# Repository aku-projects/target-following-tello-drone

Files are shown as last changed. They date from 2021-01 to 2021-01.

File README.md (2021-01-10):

# Target following tello drone

## Intro
This repo contains code to provide tello drone the capability to follow any particular target using Sipeed maix bit board. ESP32 board is used as a communication bridge between external bluetooth app, maix bit board and tello.

As examples, the scripts added here allows the drone to follow green coloured object or raccoon for which a neural network was trained

For coloured objects the drone can align itself and move towards it.

For raccoon/object it can only detect and move towards it/follow it in straight line. This mainly was due to the viewing angle and size of the object causing detection issue. Probably better training can be done to make the object following more robust.

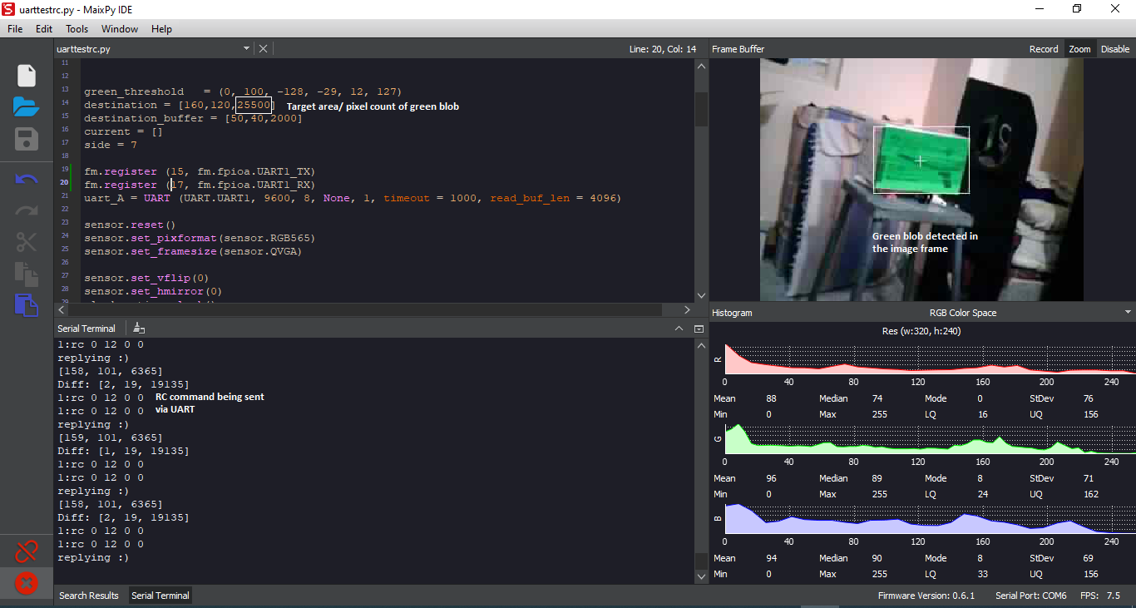
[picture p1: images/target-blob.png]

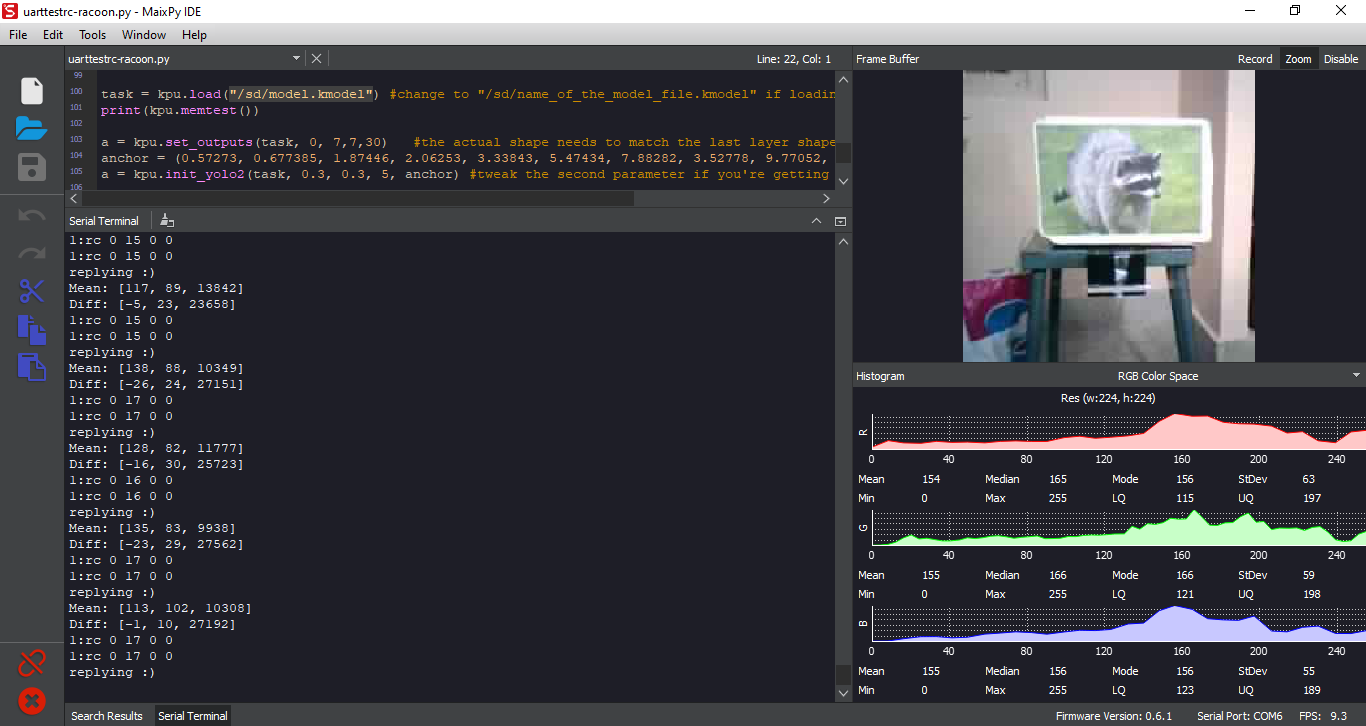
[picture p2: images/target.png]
 

## Setting up the drone

### Hardware assembly

#### Materials
1) Sipeed maix bit board (with camera) [link](https://www.seeedstudio.com/Sipeed-MAix-BiT-for-RISC-V-AI-IoT-p-2872.html)
2) ESP32 [link](https://www.amazon.com/HiLetgo-ESP-WROOM-32-Development-Microcontroller-Integrated/dp/B0718T232Z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)
3) Tello [link](https://www.amazon.com/Tello-CP-PT-00000252-01-Quadcopter-Drone/dp/B07H4W5YWB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)
4) boost converter [link](https://www.amazon.com/Comidox-Module-Voltage-Converter-0-9-5V/dp/B07L76KLRY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)
5) misc. (Wires, ziptie etc)

Mount the boards as shown in the image.  
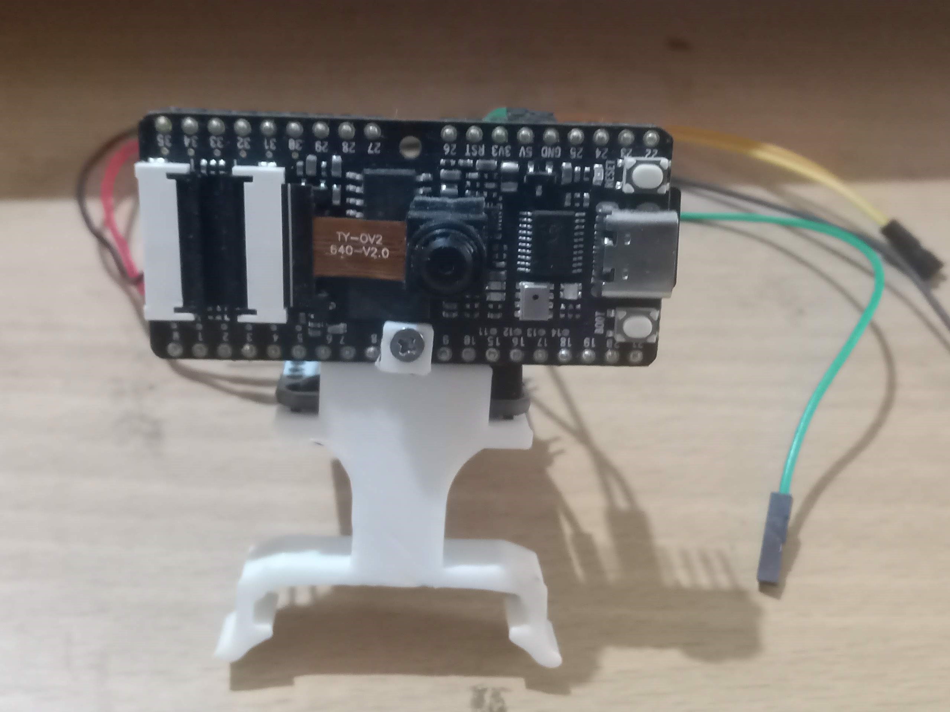
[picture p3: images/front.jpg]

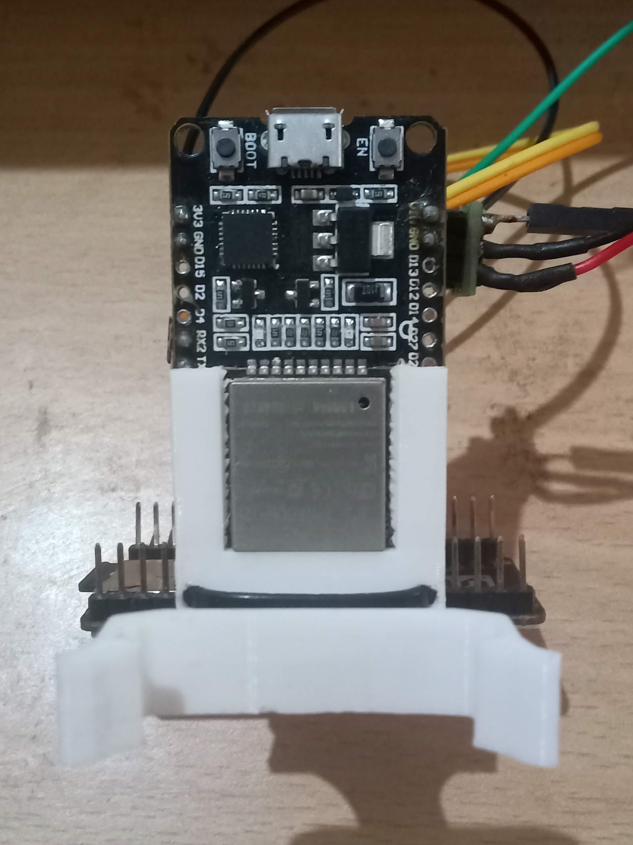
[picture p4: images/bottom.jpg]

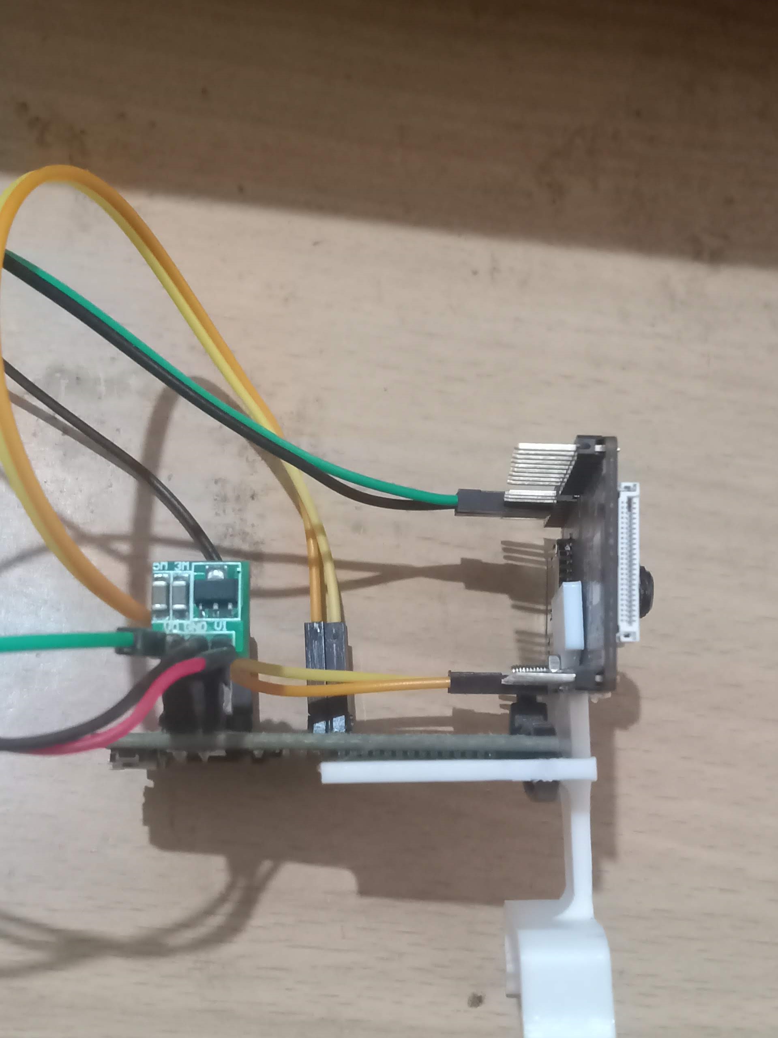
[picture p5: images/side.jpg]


Make uart connection between the Boards as follows

ESP32 GPIO 16 (UART 2 RX)<-> k210 GPIO 15 (UART 1 TX)  
ESP32 GPIO 17 (UART 2 TX)<-> k210 GPIO 17 (UART 1 RX)

Power the boards using boost converter if using 3.7 volts. For this project the 3.7 volts was tapped from on board battery.

Snap the assembly onto the tello drone
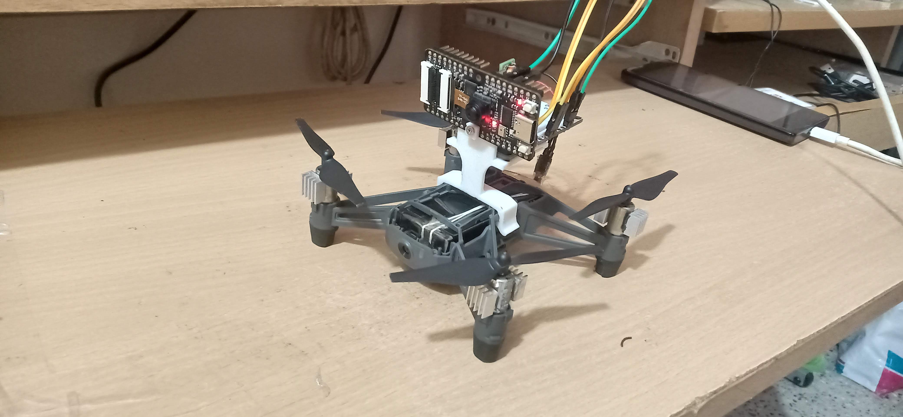
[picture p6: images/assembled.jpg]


### Software 

Create custom buttons on [Serial Bluetooth terminal app](https://play.google.com/store/apps/details?hl=en&id=de.kai_morich.serial_bluetooth_terminal) as follows:
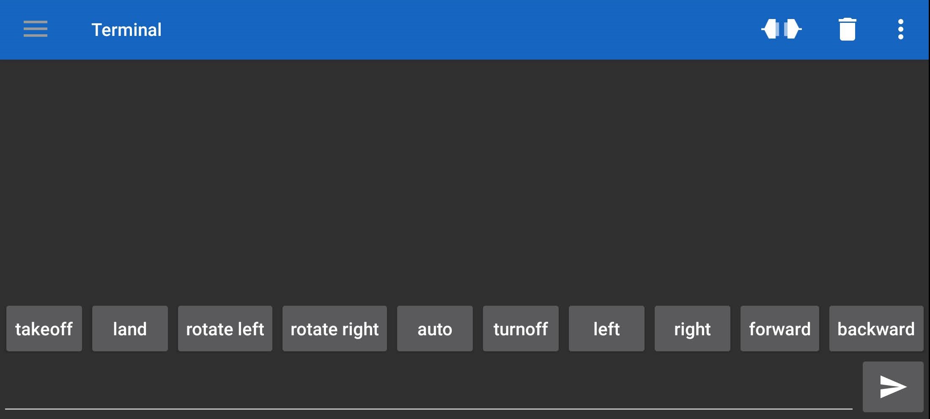
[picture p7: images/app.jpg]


add hex values for each starting from 0 ie takeoff = hex value 0, land = hex value 1, ...etc   
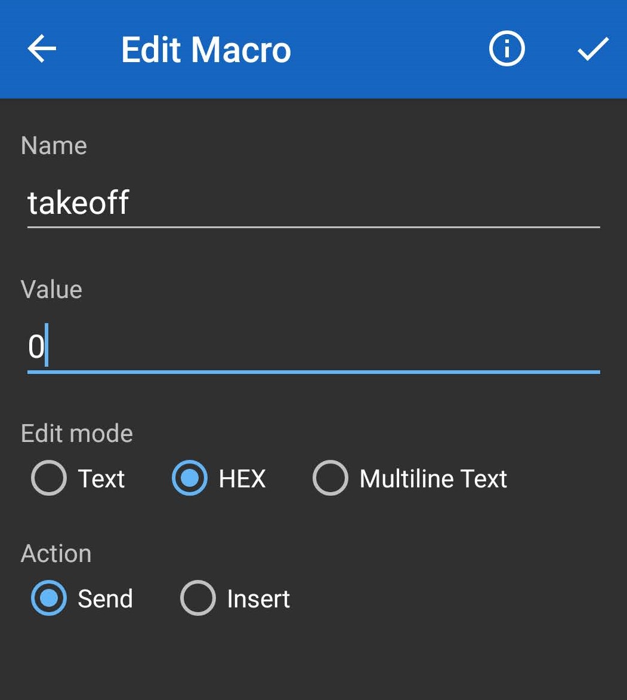
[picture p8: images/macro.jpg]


Add tello library needed by ESP32 to control the drone. [Link](https://github.com/aku-projects/ESP32-Tello)

Modify the tello wifi credentials in .ino file under resources > code > esp32 and program the same into the board.

Set up the Sipeed maix bit board based on the instructions [here.](https://maixpy.sipeed.com/en/)

Now open the micropython script in resources > code > k210 using maix py ide and save the same to the board.

use tello_rc_bt_wifi.ino and uarttestrc.[]()py for coloured object following

use tello_rc_bt_wifi_no_dest.ino and uarttestrc-racoon.[]()py for racoon following.
## Running the Code

Power up the tello drone and the boards. Connect to ESP32 using the app. Wait for ESP32 to connect to Tello wifi. 
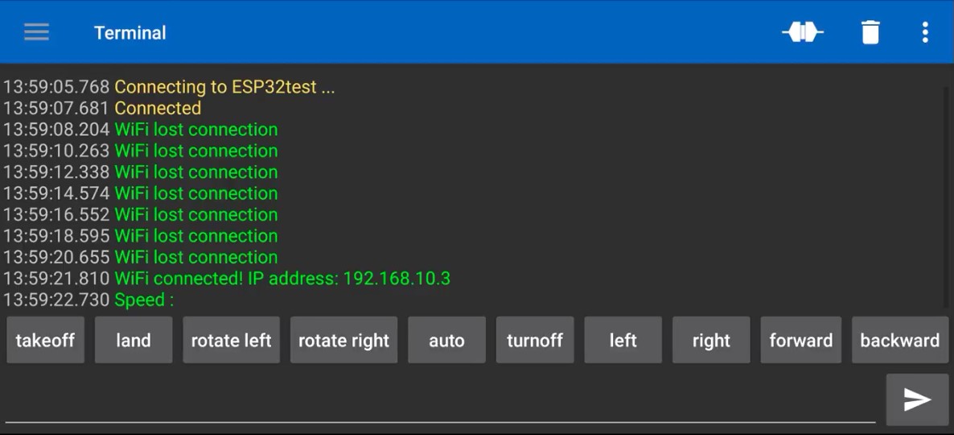
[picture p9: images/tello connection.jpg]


Once connected. Take off manually using the corresponding button on the app. Place in Auto mode using the corresponding button. If target is detected the drone makes the manuever and hovers at a set distance from it, else lands after Tello's default timeout.

## Acknowledgment
Raccoon detector was based on the work of Dmitry Maslov. The tutorial can be found at :  https://www.hackster.io/dmitrywat/object-detection-with-sipeed-maix-boards-kendryte-k210-421d55  
The tello mount used in this project is a Remix of Raspberry Pi Zero Tello mount by zeroTM on thingiverse : https://www.thingiverse.com/thing:4022999

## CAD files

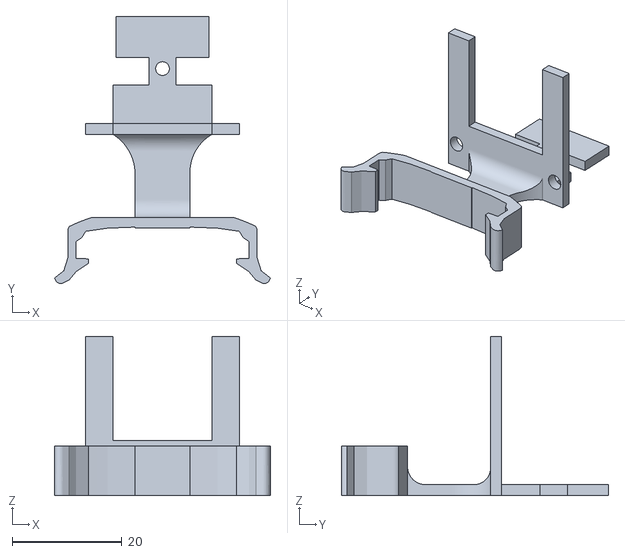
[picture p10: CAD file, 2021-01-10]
Resources/3d design/autonomousdrone3.stl
39.3 x 48.7 x 29.0

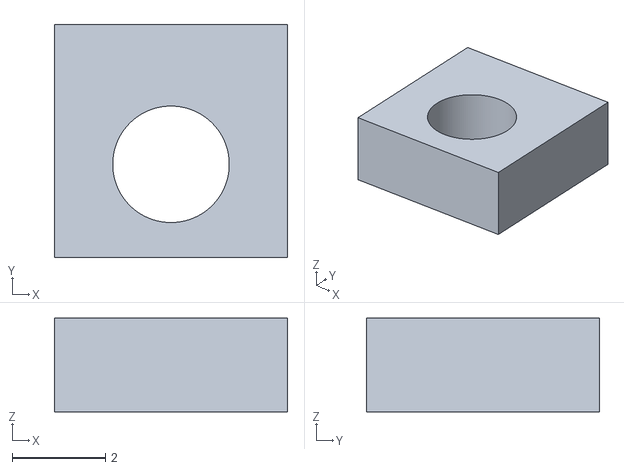
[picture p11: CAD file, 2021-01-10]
Resources/3d design/washer.stl
5.00 x 5.00 x 2.01

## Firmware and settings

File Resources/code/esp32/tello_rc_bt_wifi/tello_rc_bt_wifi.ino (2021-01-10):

#include "BluetoothSerial.h"
#include <Tello.h>


#define RXD2 16
#define TXD2 17
#define INPUT_SIZE 30

BluetoothSerial BT_SERIAL;
Tello tello;


const char * networkName = "TELLO-XXXXX";
const char * networkPswd = "";
String BT_CALLBACK = "";
String command = "";
char input;
int controlmode = 0;
boolean connected = false;




void connectToWiFi(const char * ssid, const char * pwd) 
{
  Serial.println("Connecting to WiFi network: " + String(ssid));
  BT_SERIAL.println("Connecting to WiFi network: " + String(ssid));
  WiFi.disconnect(true);
  WiFi.onEvent(WiFiEvent);
  WiFi.begin(ssid, pwd);
  Serial.println("Waiting for WIFI connection...");
  
}

void WiFiEvent(WiFiEvent_t event) 
{
  switch (event) 
  {
    case SYSTEM_EVENT_STA_GOT_IP:
      Serial.print("WiFi connected! IP address: ");
      Serial.println(WiFi.localIP());
      BT_SERIAL.print("WiFi connected! IP address: ");
      BT_SERIAL.println(WiFi.localIP());
      tello.init();
      delay(1000);
      Serial.println("Speed : "+ tello.getSpeed());
      BT_SERIAL.println("Speed : "+ tello.getSpeed());
      connected = true;
      break;
      
    case SYSTEM_EVENT_STA_DISCONNECTED:
      Serial.println("WiFi lost connection");
      BT_SERIAL.println("WiFi lost connection");
      connected = false;
      break;
  }
}



void BTCallback(esp_spp_cb_event_t event, esp_spp_cb_param_t *param)
{
    if(event == ESP_SPP_SRV_OPEN_EVT)               // CONNECTION STABLISHED
    {
        BT_CALLBACK = "BTonConnect";
    }
    else if(event == ESP_SPP_CLOSE_EVT)             // CONNECTION CLOSED
    {
        ESP.restart();
    }
    else if(event == ESP_SPP_DATA_IND_EVT)          // DATA RECEIVED
    {
        BT_CALLBACK = "BTonReceivedStart";
    }
//    else if(event == ESP_SPP_WRITE_EVT)             // DATA WRITED
//    {
//        BT_CALLBACK = "BTonWrite";
//    }
}


void BTonReceivedStart()
{
    if(BT_SERIAL.available())
    {
        input = BT_SERIAL.read();
        BT_SERIAL.flush();
        switch(input)
        {
         case 0:
          command = "takeoff";
          controlmode = 0;
          break;
         case 1:
          command = "land";
          controlmode = 0;
          break; 
         case 2:
          command = "rotate clockwise";
          controlmode = 0;
          break;
         case 3:
          command = "rotate anticlockwise";
          controlmode = 0;
          break;
         case 4:
          command = "auto";
          controlmode = 1;
          break;
         case 5:
          command = "turn off";
          controlmode = 0;
          break;
         case 6:
          command = "left";
          controlmode = 0;
          break;
         case 7:
          command = "right";
          controlmode = 0;
          break;
         case 8:
          command = "forward";
          controlmode = 0;
          break;
         case 9:
          command = "backward";
          controlmode = 0;
          break;      
        }
    }
}


 
void setup()
{
  
  Serial.begin(115200);
  BT_SERIAL.register_callback(BTCallback);
  BT_SERIAL.begin("ESP32test");
  Serial2.begin(9600, SERIAL_8N1, RXD2, TXD2);
  Serial.println("Serial Txd is on pin: "+String(TX));
  Serial.println("Serial Rxd is on pin: "+String(RX));
  BT_SERIAL.println("Serial Txd is on pin: "+String(TX));
  BT_SERIAL.println("Serial Rxd is on pin: "+String(RX));
  connectToWiFi(networkName, networkPswd);
}


void automode_run()
{
  while(controlmode)
  {

    if(connected)
    {
      Serial.println("In automode");
      BT_SERIAL.println("In automode");
      Serial2.write("1");
      delay(90);
  
      if (Serial2.available()) 
      {
        char input[INPUT_SIZE + 1];
        byte size = Serial2.readBytes(input, INPUT_SIZE);
        input[size] = 0;

        char* separator = strchr(input, ':');
        if (separator != 0)
        {

            *separator = 0;
            int tagfound = atoi(input);
            Serial.println(tagfound);
            BT_SERIAL.println(tagfound);
            if (tagfound)
            {
              Serial.println(tagfound);
              Serial.println("tagfound");
              BT_SERIAL.println(tagfound);
              BT_SERIAL.println("tagfound");
              
            }
            
            ++separator;
            Serial.println(separator);
            BT_SERIAL.println(separator);
            
            if (tagfound && (strcmp( separator, "rc 0 0 0 0" ) == 0))
             {
              Serial.println("Reached destination!"); 
              BT_SERIAL.println("Reached destination!"); 
              tello.sendCommand("rc 0 0 0 0");
              controlmode = 0;
              break;
              
             }
            tello.sendCommand(separator);
//            delay(500);
//            tello.sendCommand("rc 0 0 0 0");
            Serial.println("Sent command");
            BT_SERIAL.println("Sent command");

          }

      }
  }
  if(BT_CALLBACK=="BTonReceivedStart")
   {
    
    BTonReceivedStart();
    Serial.println(command);
    Serial.println(controlmode);
    BT_SERIAL.println(command);
    BT_SERIAL.println(controlmode);
    if (!controlmode)
    {
      tello.sendCommand("rc 0 0 0 0");
      Serial.println("manual overtake");
      BT_SERIAL.println("manual overtake");
      sendcommand(command);
    }
    BT_CALLBACK="";
    }  

  }  
}

void loop()
{ 
    if(BT_CALLBACK=="BTonReceivedStart")
    {
        BTonReceivedStart();
        Serial.println(command);
        Serial.println(controlmode);
        BT_SERIAL.println(command);
        BT_SERIAL.println(controlmode);
        sendcommand(command);
        BT_CALLBACK="";
        if(controlmode)
        {
          automode_run();  
        }
    }
}

void sendcommand(String command)
{
  if (command == "takeoff")
   {
    tello.takeoff(); 
   }
  if (command == "land")
   {
    tello.land(); 
   } 
  if (command == "rotate clockwise")
   {
    tello.rotate_clockwise(30); 
   }
  if (command == "rotate anticlockwise")
   {
    tello.rotate_anticlockwise(30);
   }
  if (command == "turn off")
   {
    tello.turnOff();
   }
  if (command == "left")
   {
    tello.left(30);
   }
  if (command == "right")
   {
    tello.right(30);
   }
  if (command == "forward")
   {
    tello.forward(30);
   }
  if (command == "backward")
   {
    tello.back(30);
   }
    
}

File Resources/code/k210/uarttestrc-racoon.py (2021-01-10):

"""rc a b c d
a left/right
b forward/backward
c up/down
d yaw """


import sensor,image
import KPU as kpu
from machine import UART
from fpioa_manager import fm

print(kpu.memtest())

classes = ["racoon"]
destination = [112,112,37500]
destination_buffer = [56,56,3000]
current = []
currentlist = []


fm.register (15, fm.fpioa.UART1_TX)
fm.register (17, fm.fpioa.UART1_RX)
uart_A = UART (UART.UART1, 9600, 8, None, 1, timeout = 1000, read_buf_len = 4096)


sensor.reset()
sensor.set_pixformat(sensor.RGB565)
sensor.set_framesize(sensor.QVGA)
sensor.set_windowing((224, 224))
sensor.set_hmirror(0)
sensor.run(1)

def mean(a):
    return int(sum(a) / len(a))

def process_target():
    global currentlist
    for x in range(6):
        img = sensor.snapshot()
        a = img.pix_to_ai()
        code = kpu.run_yolo2(task, img)
        if code:
            i = code[0]
            #print(i)
            current= [i.x()+int(i.w()/2),i.y()+int(i.h()/2),i.w()*i.h()]
            currentlist.append(current)
            #print(current)
            #print(currentlist)

    if(len(currentlist)>0):
        average = list(map(mean, zip(*currentlist)))
        print("Mean:",average)
        currentlist = []


        difference = []
        zip_object = zip(destination, average)
        for list1_i, list2_i in zip_object:
            difference.append(list1_i-list2_i)
        print("Diff:",difference)
        factor = 1

#        if abs(difference[0]) > destination_buffer[0]:
#            if (difference[0] > 0):
#                factor = -1
#            if abs(average[2]) > 9000:
#                print("1:rc "+str(int(12*factor*(difference[2]/destination[2])))+" 0 0 0")
#                return "1:rc "+str(int(12*factor*(difference[2]/destination[2])))+" 0 0 0"
#            else:
#            print("1:rc 0 0 0 "+str(int(12*factor*(difference[2]/destination[2]))))
#            return "1:rc 0 0 0 "+str(int(12*factor*(difference[2]/destination[2])))

#        if abs(difference[1]) > destination_buffer[1]:
#            if (difference[1] < 0):
#                factor = -1
#            print("1:rc 0 0 "+str(int(15*factor*(difference[2]/destination[2])))+" 0")
#            return "1:rc 0 0 "+str(int(15*factor*(difference[2]/destination[2])))+" 0"

        if abs(difference[2]) > destination_buffer[2]:
            if (difference[2] < 0):
                factor = 0

            print("1:rc 0 "+str(int((24*(difference[2]/destination[2]))*factor))+" 0 0")
            return "1:rc 0 "+str(int((24*(difference[2]/destination[2]))*factor))+" 0 0"
        print("1:rc 0 0 0 0")
        return "1:rc 0 0 0 0"
    else:
        print("0:rc 0 0 0 0")
        return "0:rc 0 0 0 0"

def run_algo():

    print("replying :)")
    rccommand = process_target()
    print(rccommand)
    uart_A.write(rccommand)


task = kpu.load("/sd/model.kmodel") #change to "/sd/name_of_the_model_file.kmodel" if loading from SD card
print(kpu.memtest())

a = kpu.set_outputs(task, 0, 7,7,30)   #the actual shape needs to match the last layer shape of your model(before Reshape)
anchor = (0.57273, 0.677385, 1.87446, 2.06253, 3.33843, 5.47434, 7.88282, 3.52778, 9.77052, 9.16828)
a = kpu.init_yolo2(task, 0.3, 0.3, 5, anchor) #tweak the second parameter if you're getting too many false positives

while(True):
    #if uart_A.any():
        #try:

            #read_data = uart_A.read()
            #read_str = read_data.decode('utf-8')
            #if (read_str == "1"):
                #print("string = ", read_str)
                #run_algo()
        #except  (UnicodeError):
            #pass
     run_algo()


a = kpu.deinit(task)
